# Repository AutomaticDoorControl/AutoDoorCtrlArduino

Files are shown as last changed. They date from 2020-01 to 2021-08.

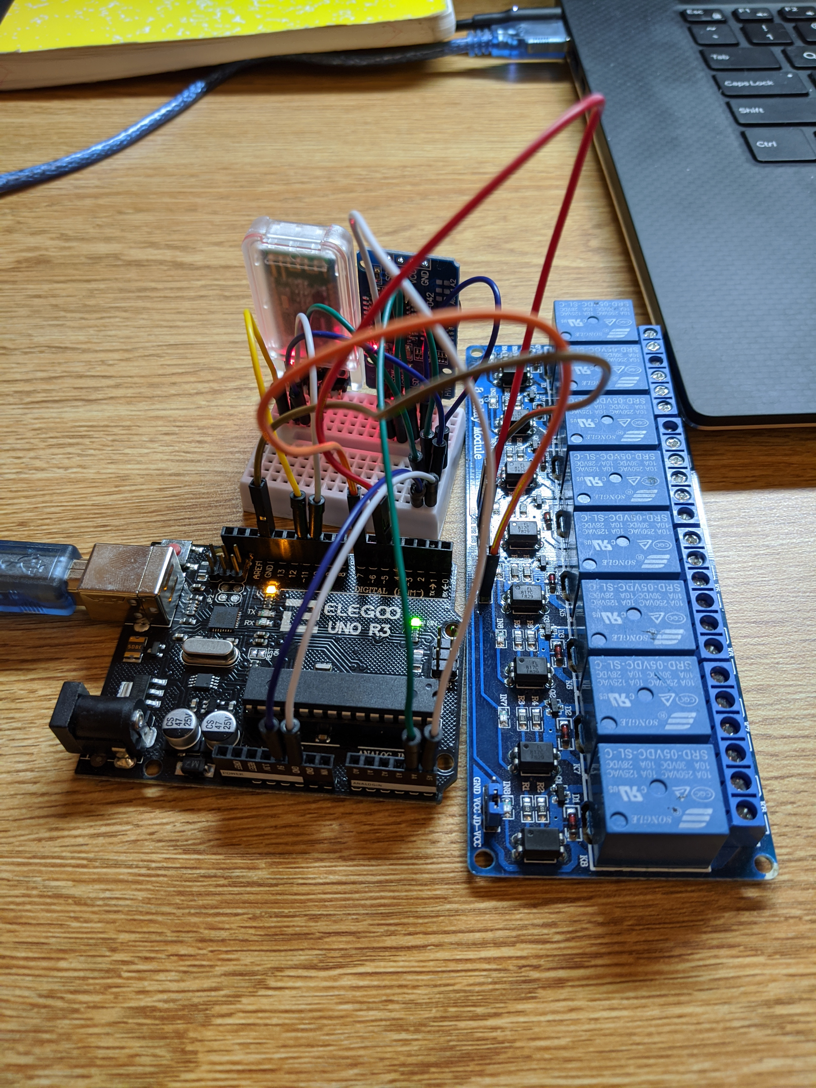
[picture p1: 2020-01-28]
Circuit_Diagrams/ADC_arduino.jpg

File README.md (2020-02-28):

# Automatic Door Control Arduino
Main repository of all Arduino-related files and programs belonging to the ADC project.
The Arduino portion of the ADC project is tasked with recieving a 6 digit TOTP over bluetooth, comparing the TOTP to one generated using the onboard RTC and HMAC private key, and if the TOTP matches firing a relay to trigger the door opening.

## How to Wire HC-08: (Also shown in Circuit_Diagrams/ADC_circuit)
1. VCC goes to 5V power supply on arduino
2. GND goes to ground power on arudino
3. TXD goes to Digital pin 10 on arduino
4. RXD goes to Digital pin 11 on arduino
5. The other two (State and FN) don't touch

## How to wire the RTC: (also shown in Circuit_Diagrams/ADC_Circuit)
1. GND goes to the ground on the arduino
2. VCC goes to the 3.5V power supply (5V also works but recommended use is 3.5V)
3. SDA goes to Analogin Pin A4
4. SCL goes to Analogin Pin A5
5. 32K and SQW don't touch

## How to set the current time using the RTC and Linux
1. Upload the RTC.ino sketch to the Arduino
2. While running and connected, run `date +T%s > /dev/ttyUSB0` to send the current UTC time to the Arduino

## How to setup Arduino:

1. Wire the arduino up correctly
3. First set up the time to the RTC by uploading RTC.ino to the arduino and setting the current time in the code
4. Next you might want to rename the HC-08 so you can add it to the API. The code rename.ino can help with renaming the HC-08 module
5. Last step is to upload the TOTP_ADC code and select the correct key for the specific door

## Dependencies
- https://github.com/lucadentella/TOTP-Arduino/tree/master/ for TOTP generation
- https://github.com/JChristensen/DS3232RTC for the RTC
- https://github.com/PaulStoffregen/Time for Arduino time

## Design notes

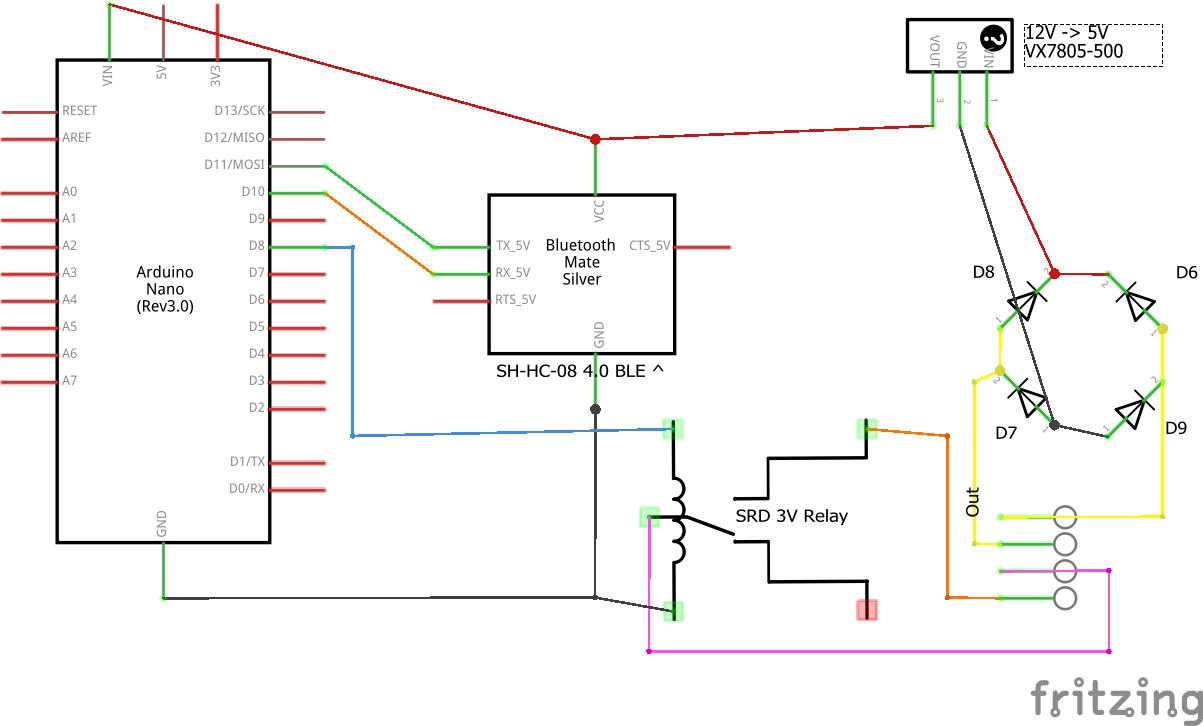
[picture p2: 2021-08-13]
Circuit_Diagrams/BLE3_schem.jpg

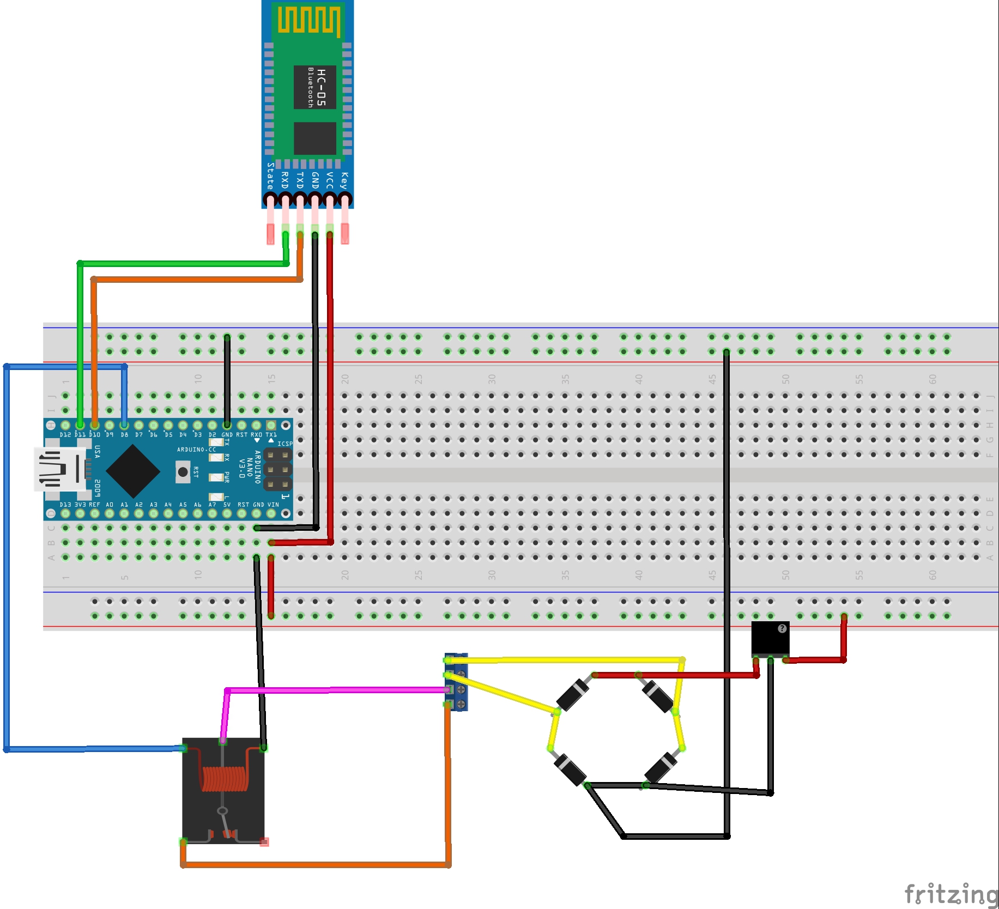
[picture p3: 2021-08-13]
Circuit_Diagrams/BLE3_bb.jpg

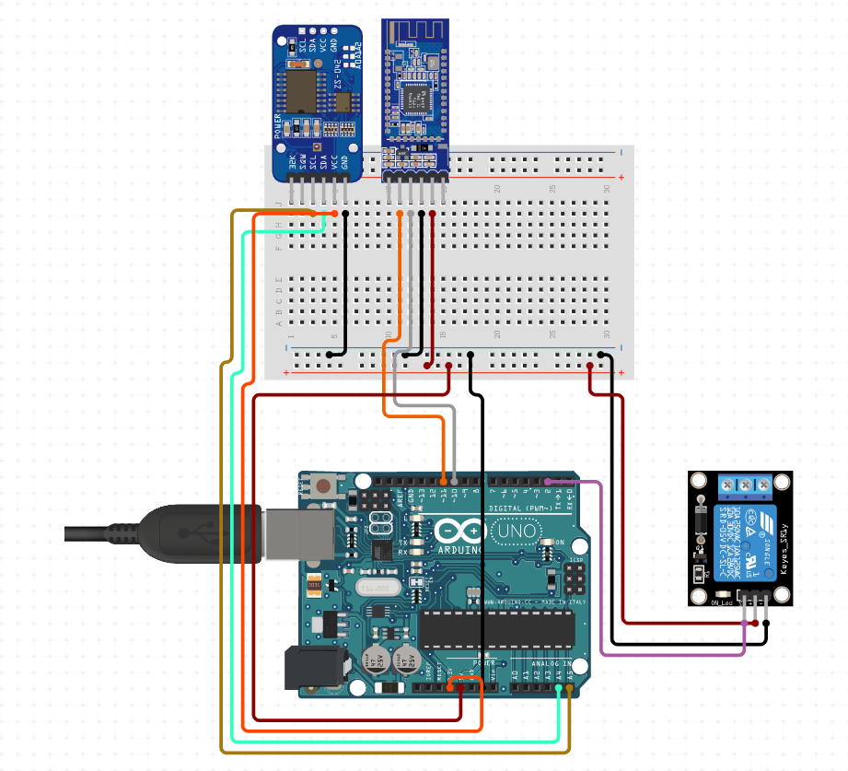
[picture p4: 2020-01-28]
Circuit_Diagrams/ADC_circuit.PNG

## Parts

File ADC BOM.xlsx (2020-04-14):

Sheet: BillOfMaterials
Automatic Door Control
 | Assembly Name : | N/A |  |  | [42]
 | Assembly Number : | 1
 | Assembly Revision : | Rev01
 | Approval Date : | N/A
 | Part Count : | 6
 | Total Cost : | $42.90
Part # | Part Name | Description | Qty | Units | Picture | Unit Cost | Cost | Link to Purchase
 | RTC& EEPROM Module DS3231 AT24C32 | low-cost, accurate I2C real-time clock (RTC), | 1 |  |  | $3.00 | $3.00 | https://www.elecrow.com/rtc-eeprom-module-ds3231-at24c32-p-863.html
 | Relay SPDT Sealed | 12V max, 5V min, max 5A used to switch high voltage | 1 |  |  | $1.95 | $1.95 | https://www.sparkfun.com/products/100
 | Arduino Nano V3 | Microcontroller: ATmega328 Operating Voltage (logic level): 5V Input Voltage (recommended): 7V ~ 12V Input Voltage (limits): 6V ~ 20 V | 1 |  |  | $5.87 | $5.87 | https://www.banggood.com/ATmega328P-Nano-V3-Module-Improved-Version-No-Cable-Development-Board-p-959231.html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
 | LM2596 DC-DC (Not Finalized yet) | Input: DC 3V to 40V (input voltage must be higher than the output voltage to 1.5v above can not boost) | 1 |  |  | $14.95 | $14.95 | https://www.amazon.com/LM2596-Converter-Module-Supply-1-23V-30V/dp/B008BHBEE0
 | DSD TECH SH-HC-08 Bluetooth 4.0 BLE1 | Output: DC 1.5V to 35V voltage continuously adjustable, high-efficiency maximum output current of 3A. | 1 |  |  | $7.99 | $7.99 | https://www.amazon.com/DSD-TECH-SH-HC-08-Transceiver-Compatible/dp/B01N4P7T0H
 | PCB (Fritzing) | PCB through Vendor | 1 |  |  | $9.14 | $9.14 | https://aisler.net/partners/fritzing
 |  |  |  |  |  |  | $0.00
 |  |  |  |  |  |  | $0.00
 |  |  |  |  |  |  | $0.00
 |  |  |  |  |  |  | $0.00
 |  |  |  |  |  |  | $0.00
 |  |  |  |  |  |  | $0.00
 |  |  |  |  |  |  | $0.00
 |  |  |  |  |  |  | $0.00
 |  |  |  |  |  |  | $0.00
 |  |  |  |  |  |  | $0.00
 |  |  |  |  |  |  | $0.00
 |  |  |  |  |  |  | $0.00
 |  |  |  |  |  |  | $0.00
 | Total |  | 6 |  |  |  | $42.90

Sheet: Revisions
Revision History
 | Assembly Name :
 | Assembly Number :
Revision | Revision Summary | Approval Date

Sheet: Example
Bill of Materials for LEGO® Design
 |  |  | https://www.vertex42.com/ExcelTemplates/free-timesheet-template.html |  |  |  |  |  |  | © 2012-2019 Vertex42 LLC
 |  |  | Assembly Name : | Mini X-Wing™ |  |  | [42] |  |  | Bill of Materials Template (https://www.vertex42.com/ExcelTemplates/bill-of-materials.html)
 |  |  | Assembly Number : | Custom
 |  |  | Assembly Revision :
 |  |  | Approval Date :
 |  |  | Pieces : | 46
 |  |  | Total Cost : | $5.85
Category | Part # | Elem ID | Part Name | Color | Qty | Units | Picture | Unit Cost | Cost
Bricks, Sloping | 50746 | 4504369 | ROOF TILE 1X1X2/3, ABS | 1 - White | 1 | each |  | $0.10 | $0.10
Plates | 3024 | 302401 | PLATE 1X1 | 1 - White | 1 | each |  | $0.10 | $0.10
Plates | 3023 | 302301 | PLATE 1X2 | 1 - White | 2 | each |  | $0.10 | $0.20
Plates | 3023 | 4211398 | PLATE 1X2 | 194 - Medium Stone Grey | 1 | each |  | $0.10 | $0.10
Plates | 3794 | 379401 | PLATE 1X2 W. 1 KNOB | 1 - White | 1 | each |  | $0.10 | $0.10
Plates | 3623 | 362301 | PLATE 1X3 | 1 - White | 1 | each |  | $0.10 | $0.10
Plates | 3623 | 362321 | PLATE 1X3 | 21 - Bright Red | 1 | each |  | $0.10 | $0.10
Plates | 94148 | 302201 | PLATE 2X2 | 1 - White | 1 | each |  | $0.15 | $0.15
Plates, Special | 6141 | 4210633 | PLATE 1X1 ROUND | 199 - Dark Stone Grey | 1 | each |  | $0.10 | $0.10
Plates, Special | 3070 | 307021 | FLAT TILE 1X1 | 21 - Bright Red | 4 | each |  | $0.10 | $0.40
Plates, Special | 2412 | 241201 | RADIATOR GRILLE 1X2 | 1 - White | 1 | each |  | $0.10 | $0.10
Plates, Special | 6019 | 4538353 | PLATE 1X1 W/HOLDER VERTICAL | 1 - White | 4 | each |  | $0.15 | $0.60
Plates, Special | 2431 | 4558168 | FLAT TILE 1X4 | 1 - White | 1 | each |  | $0.20 | $0.20
Plates, Special | 63868 | 4535737 | PLATE 2X1 W/HOLDER,VERTICAL | 1 - White | 4 | each |  | $0.15 | $0.60
Plates, Special | 2540 | 4211632 | PLATE 1X2 W. STICK | 194 - Medium Stone Grey | 4 | each |  | $0.15 | $0.60
Plates, Special | 3176 | 4225733 | COUPLING PLATE 2X2 | 199 - Dark Stone Grey | 1 | each |  | $0.20 | $0.20
Bricks, Special | 49668 | 4224793 | PLATE 1X1 W/TOOTH | 5 - Brick Yellow | 1 | each |  | $0.10 | $0.10
Technic | 32123 | 4211573 | 1/2 BUSH | 194 - Medium Stone Grey | 4 | each |  | $0.10 | $0.40
Technic | 6590 | 4211622 | BUSH FOR CROSS AXLE | 194 - Medium Stone Grey | 8 | each |  | $0.15 | $1.20
Accessories | 3957 | 4211473 | STICK/AERIAL | 194 - Medium Stone Grey | 4 | each |  | $0.10 | $0.40
 |  |  | Total |  | 46 |  |  |  | $5.85

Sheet: ©
Bill of Materials Template
By Vertex42.com
https://www.vertex42.com/ExcelTemplates/bill-of-materials.html
© 2012-2019 Vertex42 LLC
This spreadsheet, including all worksheets and associated content is a copyrighted work under the United States and other copyright laws.
Do not submit copies or modifications of this template to any website or online template gallery.
Please review the following license agreement to learn how you may or may not use this template. Thank you.
License Agreement
https://www.vertex42.com/licensing/EULA_privateuse.html
Do not delete this worksheet

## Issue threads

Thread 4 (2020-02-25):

Update RTC setup

bsakai2000, 2020-02-25:
https://forum.arduino.cc/index.php?topic=367987.msg2536880#msg2536880 provides example code for getting time from a laptop. This would likely allow us to set the arduino system clock and subsequently the RTC using a laptop's system clock. This would reduce error while setting the RTC

Closed 2020-02-28.

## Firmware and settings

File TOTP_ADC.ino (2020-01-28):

#include <sha1.h>     //sha1.h and TOTP.h allow for TOTP authentification
#include <TOTP.h>
#include <DS3232RTC.h>  //https://github.com/JChristensen/DS3232RTC
#include <SoftwareSerial.h>

//Key for -ADC-
uint8_t hmacKey[] = {0xb8, 0x52, 0xaf, 0xc9, 0x91, 0x82, 0x5b, 0xf9, 0x72, 0x8f, 0x99, 0xd1, 0x31, 0x65, 0xc1, 0xe5, 0xde, 0xe8, 0xd2, 0xea, 0x71, 0xa7, 0x63, 0x39, 0x38, 0x24, 0xe1, 0xe2, 0x94, 0xd2, 0x29, 0x3f};

//Key for -SAGE_SOUTH-
//uint8_t hmacKey[] = {0x6d, 0x64, 0x3f, 0x8b, 0xda, 0xeb, 0xf8, 0x7a, 0x45, 0x72, 0x27, 0x12, 0x78, 0x48, 0xca, 0x91, 0xfd, 0xf1, 0x7e, 0x94, 0xa3, 0x28, 0x7e, 0x91, 0xb6, 0xe5, 0x3f, 0xa1, 0xec, 0xf6, 0x1a, 0xe0};

//Key for -LALLY_NORTH-
//uint8_t hmacKey[] = {0xe0, 0x56, 0x37, 0xef, 0xed, 0xff, 0xae, 0x61, 0x2b, 0x9b, 0x03, 0x1c, 0x03, 0xa4, 0x62, 0x3c, 0xfa, 0xcf, 0x70, 0x6c, 0xdf, 0x4f, 0xe7, 0x02, 0xba, 0x3e, 0x4e, 0xfa, 0x66, 0xd8, 0xc0, 0x60};

//Key for -SAGE_EAST-
//uint8_t hmacKey[] = {0xf1, 0x83, 0x92, 0xef, 0xa0, 0x7c, 0x46, 0x92, 0x64, 0x4b, 0x86, 0xa1, 0xc5, 0x4b, 0xf3, 0xbd, 0xf5, 0xf8, 0x24, 0xfc, 0x5d, 0x25, 0xd6, 0xc9, 0xf5, 0x15, 0xd6, 0x7b, 0x38, 0x1b, 0x4a, 0x59};

//Set up variables
TOTP totp = TOTP(hmacKey, 32);
TOTP totp_past = TOTP(hmacKey, 32);
TOTP totp_future = TOTP(hmacKey, 32);
String temp;
String code;
#define DOOR_PIN 5
#define txPin 11
#define rxPin 10
#define timeError 20

SoftwareSerial adc(rxPin, txPin);

void setup() {
    //Supply 
    pinMode(7, OUTPUT);
    digitalWrite(7, HIGH);
    pinMode(DOOR_PIN, OUTPUT);
    digitalWrite(DOOR_PIN, HIGH);
    pinMode(rxPin, INPUT);
    pinMode(txPin, OUTPUT);
    Serial.begin(9600);
    adc.begin(9600);
    
    //If time gets messed up you need to reset it (takes about 7 seconds to upload)
//  setTime(13, 45, 0, 1, 11, 2019);
//  RTC.set(now());
    
    setSyncProvider(RTC.get);   // the function to get the time from the RTC
    if(timeStatus() != timeSet)
        Serial.println("Unable to sync with the RTC");
    else
        Serial.println("RTC has set the system time");
  
  // Adjust the following values to match the current date and time
  // and power on Arduino at the time set (use GMT timezone!)
}

void loop() {
  //Loops when recieves an input
  if(adc.available()){
    code = "";
    temp = adc.readString();
//    adc.print(temp);
    for(int i=0; i < 6; i++){
        code += temp[i];
    }
    //Time since epoch
    time_t current_time =  RTC.get();
    time_t past_time = current_time - timeError;
    time_t future_time = current_time + timeError;
    //Print info to make sure GMT timezone is correct
    printGMT();
    //Get the code
    char* newCode = totp.getCode(current_time);
    char* past = totp_past.getCode(past_time);
    char* future = totp_future.getCode(future_time);
    String correct(newCode);
    String past_correct(past);
    String future_correct(future);
    if(code.equals(correct) || code.equals(past_correct) || code.equals(future_correct)) {
      Serial.println("Door Open");
//      adc.println("OPEN");
      digitalWrite(DOOR_PIN, LOW);
      delay(2000);
      digitalWrite(DOOR_PIN, HIGH);
      Serial.println("Door is now closing");
      adc.println("CLOSED");
    }  
    else{
      Serial.println("Invalid token");
      adc.println("INVALID TOKEN");
    }
    Serial.println(code);
    Serial.println(correct);
  }
}


void printDigits(int digits)
{
    // utility function for digital clock display: prints preceding colon and leading 0
    Serial.print(':');
    if(digits < 10)
        Serial.print('0');
    Serial.print(digits);
}

void printGMT(){
    Serial.print(hour());
    printDigits(minute());
    printDigits(second());
    Serial.print(' ');
    Serial.print(day());
    Serial.print(' ');
    Serial.print(month());
    Serial.print(' ');
    Serial.print(year());
    Serial.println();
}

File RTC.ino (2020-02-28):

// Portions of this code adapted from https://forum.arduino.cc/index.php?topic=367987.msg2536880#msg2536880

// https://github.com/JChristensen/DS3232RTC, provides functions for
//interacting with RTC
#include "DS3232RTC.h"

// Time values sent over serial should be prefixed with a T to
// ensure we're getting the right values over serial
#define TIME_HEADER  "T"

// STart the program by notifying the user that we're ready to recieve
void setup()
{
	Serial.begin(9600);
	Serial.println("Waiting for sync message");
}

// Every second, check for a new time and update the current time with it.
// Otherwise, print the current time.
void loop()
{
	if (Serial.available()) {
		processSyncMessage();
	}
	if (timeStatus()!= timeNotSet) {
		digitalClockDisplay();  
	}
	delay(1000);
}

// Print the current time and date
void digitalClockDisplay()
{
	// digital clock display of the time
	Serial.print("GMT Time: ");
	Serial.print(hour());
	printDigits(minute());
	printDigits(second());
	Serial.print(' ');
	Serial.print(day());
	Serial.print(' ');
	Serial.print(month());
	Serial.print(' ');
	Serial.print(year());
	Serial.println();
}

// Print an int as a two digit number prefixed by a colon
void printDigits(int digits)
{
	Serial.print(':');
	// If our value is less than 10, pad with a 0
	if(digits < 10)
		Serial.print('0');
	Serial.print(digits);
}

// Get the message sent over serial and use it to set the current time and RTC
void processSyncMessage() {
	unsigned long pctime;
	const unsigned long DEFAULT_TIME = 1357041600; // Jan 1 2013

	// Make sure this is a time transmission
	if(Serial.find(TIME_HEADER))
	{
		// Read the time, and if valid set the current time and RTC
		pctime = Serial.parseInt();
		if( pctime >= DEFAULT_TIME) { // check the integer is a valid time (greater than Jan 1 2013)
			setTime(pctime); // Sync Arduino clock to the time received on the serial port
			RTC.set(now()); // Set RTC to the current value of the Arduino clock
		}
	}
}

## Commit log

2018-11-13 Diagrams for Bluetooth (BLE) Circuit
    [BLE.fzz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]
2019-09-19 Working Arduino Code
2020-02-14 Deleted old files and updated README
    [BLE.fzz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]
2020-04-14 Add files via upload
    Introduces Rev01 Bill of Materials for Hardware
    [ADC BOM.xlsx]
2021-08-13 Gerber files for circuit
    Ready for PCB
2021-08-13 Added CERN Permissive Open Hardware Liscense
    Open Source License for gerber files and general circuit design
2021-08-13 CERN Permissive Open Hardware Liscense
    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
2021-08-13 Move CERN Liscense to Circuit Diagram folder
